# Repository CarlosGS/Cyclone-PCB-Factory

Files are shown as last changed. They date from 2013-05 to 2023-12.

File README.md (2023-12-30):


<p align="center">
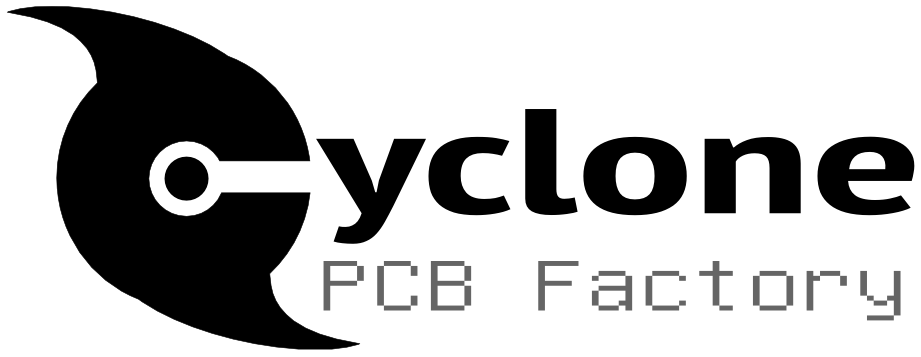
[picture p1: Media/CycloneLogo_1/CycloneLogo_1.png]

<div align="center"><i>A 3D-printable (Rep-Rap alike) CNC machine, intended for PCB manufacture.</i></div>
</p>  

Read this, it's important!
-----------

Please note that this project is no longer active and is of historical interest only.
===========

Check out this thread before printing the parts: <https://github.com/CarlosGS/Cyclone-PCB-Factory/issues/57>

**Also take a look at the following locations:**

- **Releases: <https://github.com/carlosgs/Cyclone-PCB-Factory/releases>**
- **Documentation: <https://github.com/carlosgs/Cyclone-PCB-Factory/wiki>**

<p align="center">
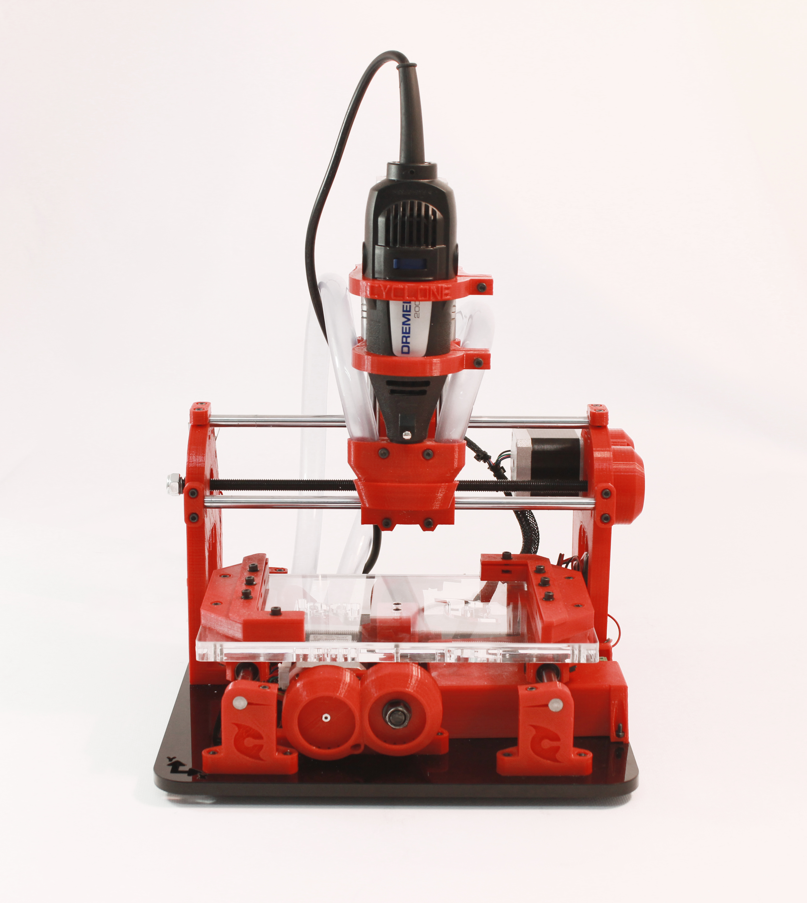
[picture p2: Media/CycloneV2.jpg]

<div align="center"><i>Cyclone v2. Picture by bq</i></div>
</p>

Mail list / Forum  
-------------------
If you are interested in this project, please consider joining our mail list:  
**English: <https://groups.google.com/forum/#!forum/cyclone-pcb-factory>**  
**Spanish/Español: <https://groups.google.com/forum/#!forum/cyclone-pcb-factory-es>**  

Links of interest  
====================
- **[GitHub project network](https://github.com/carlosgs/Cyclone-PCB-Factory/network)** (useful to find the latest work by collaborators)
- **[Wiki entry on RepRap.org](http://reprap.org/wiki/Cyclone_PCB_Factory)**
- **[Joco's Cyclone journey in the mail list](https://groups.google.com/forum/#!topic/cyclone-pcb-factory/o_YzXokpLnA)**
- **[A year of development (Jan/2014)](https://web.archive.org/web/20150627040708/http://carlosgs.es/node/47)** (project evolution during 2013)
- **[List of suppliers](https://github.com/carlosgs/Cyclone-PCB-Factory/wiki/List-of-suppliers)**

Getting the (development) source files  
========================================
Install git (http://git-scm.com/) onto your system. Then run a clone:

	git clone git://github.com/carlosgs/Cyclone-PCB-Factory.git

This will download the latest sources into a directory named 'Cyclone-PCB-Factory'.  

Current stable version: 2.1  
--  

**Recent news:**
* [Kris Wauters](http://www.digitalplayground.be/) has designed [a set of feet](http://www.thingiverse.com/thing:1131591) that raise up the machine and allow to place the electronics underneath. He has also made a [Z endstop support](http://www.thingiverse.com/thing:1131591). Check out his beautiful build in [his blog](http://www.digitalplayground.be/?p=3255).
* Introductory tutorial: [**Milling a bowl with bCNC**](https://github.com/carlosgs/grblForCyclone/wiki/2%29-Hello-World!-Mill-a-bowl-with-bCNC) (**implemented support for GRBL firmware in RAMPS and Sanguinololu** 3D printer electronics. GRBL is better for CNCs than Marlin).
* Released [**Cyclone XL (beta)**](Output_files/Cyclone_XL) with a milling area of **500x250mm**.
* BQ additions have been re-incorporated into the main parametric design (zip-ties in the Y carriage linear bearing holders, longer Z motor gear, same orientation for the Y rod idlers).
* If you use RAMPS, you may want to try this [GRBL mod](https://github.com/carlosgs/grblForCyclone), it is better than Marlin. Control it with the [bCNC](https://github.com/vlachoudis/bCNC) graphical interface.
* Z carriage modified for Dremel 3000 by [Nicolas Arias](https://groups.google.com/forum/#!msg/cyclone-pcb-factory/mfZC0KEy7gw/TaSLBKO9QJUJ) and [Marcos Bladauskas](https://groups.google.com/forum/#!msg/cyclone-pcb-factory/WJLWC5qAm-w/70eSQ2DBCAAJ) ([download it here](Output_files/Zcarriages)).
* Check out the [Arduino CNC shield housing](http://www.thingiverse.com/thing:929981) by Oliver Kreuzenbeck (Helicon).
* [Source code improvements (better parameterization, M4 screw version)](https://github.com/carlosgs/Cyclone-PCB-Factory/pull/33) by [Arne Durr (D-Byte)](https://github.com/D-Byte).
* An [**aluminium spindle holder**](https://github.com/carlosgs/Cyclone-PCB-Factory/pull/40) by [Marc Muntada (quikshot)](https://github.com/quikshot) ([download it here](Output_files/Zcarriages)).
* There is also [a folder](bq_additions) with the version by [Pedro de Oro](https://github.com/PedroDeOro) and [Luis Díaz](http://diwo.bq.com/author/ldiaz/) from **bq**, with some additions that simplify the assembly process (these have already been merged into the main branch).
* Daniel Evrard has [assembled Cyclone in Sketchup](https://groups.google.com/forum/#!msg/cyclone-pcb-factory/1TpFxE7avRo/EBSx7ouy9GwJ) which can be very useful as a template.
* Thanks must also go to [ve3sjk](https://github.com/ve3sjk), [joco-nz](https://github.com/joco-nz), Aisflow, Yiannis Mandravellos, Samuel Kranz and [yOPERO](https://github.com/yOPERO) for their constructive discussions and continuous support.
* If your printer is too small to print the main frames of the machine, take a look at the [**shorter version of the frames**](Output_files/ShorterVersion) (thanks [Burt Bicksler!!](https://groups.google.com/forum/#!msg/cyclone-pcb-factory/ue6NiWs713w/A7_4h4Ynf54J)).

**Cyclone PCB Factory V2.0 was developed in the department of innovation and robotics at [bq](http://www.bq.com/)**  
**V2.0** addressed all the issues from the original design, and implementing improvements by yOPERO, Martin Zabojnik and others:  

* More robust design with tougher parts:
 * Better holders for the linear bearings (vibration made them slide away)
 * Reinforced nut/screw holders
* Anti-backlash mechanisms
* Improved gears with smoother edges
* Protective cover for the gears
* Attachment for a vacuum cleaner
* Better scalability (parameterized design)
* Using a [Dremel 200](http://www.dremel.com/en-us/tools/Pages/ToolDetail.aspx?pid=200+Series) as the spindle motor
* Integrated endstop holders

<p align="center">
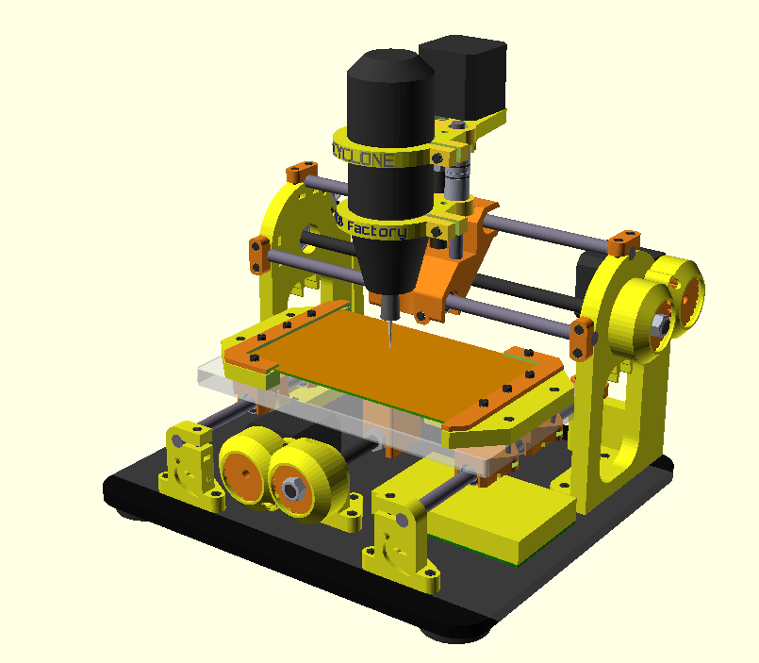
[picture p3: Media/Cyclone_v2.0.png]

<div align="center"><i>Render of Cyclone v2.0</i></div>
</p>  

<p align="center">
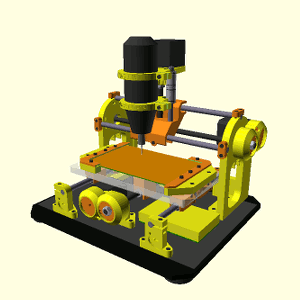
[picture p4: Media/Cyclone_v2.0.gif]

<div align="center"><i>The new design tries to be more parameterized</i></div>
</p>

Videos  
--  
- October 2015. Full milling process with bCNC, by Carlosgs: <https://www.youtube.com/watch?v=tWrt1B1CeP0>
- September 2015. Cyclone PCB jogging and homing test with bCNC, by Ianmcmill: <https://www.youtube.com/watch?v=GqbSjCq_hWg>
- July 2015. v2.0 Milling a PCB, timelapse by Helicon007: <https://www.youtube.com/watch?v=GpFG2Z8Jt-w>
- April 2015. Cyclone PCB Factory belt drive, by Nihilianth: <https://www.youtube.com/watch?v=bdu1vz6ndGs>
- April 2015. Introduction & assembly tips, by Project23D: <https://www.youtube.com/watch?v=0mW087ijIdE>
- v2.0 Plexiglass "Open Source Hardware" keychain: <http://www.youtube.com/watch?v=3Kftgog89wQ>
- v2.0 Cyclone Logo in PCB (October 2014): <http://www.youtube.com/watch?v=_6oWuco_N8U>
- v2.0a Plexiglass Cyclone logo (August 2014): <http://www.youtube.com/watch?v=lPQlIvBf7Ak>
- v2.0a Milling wax (August 2014): <http://www.youtube.com/watch?v=drV_r_OSsi4>
- February 2014. First drawing test with the Cyclone PCB Factory CNC, by Samuel Ureta: <https://www.youtube.com/watch?v=F7SczbShmxA>
- December 2013. Adjustment of Cyclone PCB Factory Y Stepper Motor Current, by Glen Chung: <https://www.youtube.com/watch?v=-TPqWOsY0Ls>
- v0.9.7 Cyclone PCB factory, the process (June 2013): <http://www.youtube.com/watch?v=fKW3fwy1h0k>
- v0.9.6 Y axis concept by yOPERO <http://www.youtube.com/watch?v=XzcobonQP40>
- v0.9.5 Probing a PCB <http://www.youtube.com/watch?v=m5zXL8k5T9E>
- v0.9.5 Milling MDF <http://www.youtube.com/watch?v=2QpxjheEjEc> and <http://www.youtube.com/watch?v=zjav0hBtmYA>
- v0.8 Drawing test: <http://www.youtube.com/watch?v=Y-HSdE89JOM>
- v0.7.5 XY axis test: <http://www.youtube.com/watch?v=9umlq4oHG64>
- v0.7.5 High speed XY test: <http://www.youtube.com/watch?v=H3uYCXryj60>

- October 2015. Evolution of the Cyclone-PCB-Factory GitHub repository (Gource Visualization), by Landon Wilkins: <https://www.youtube.com/watch?v=0ANaGCHkaco>

More pictures  
--  

<p align="center">
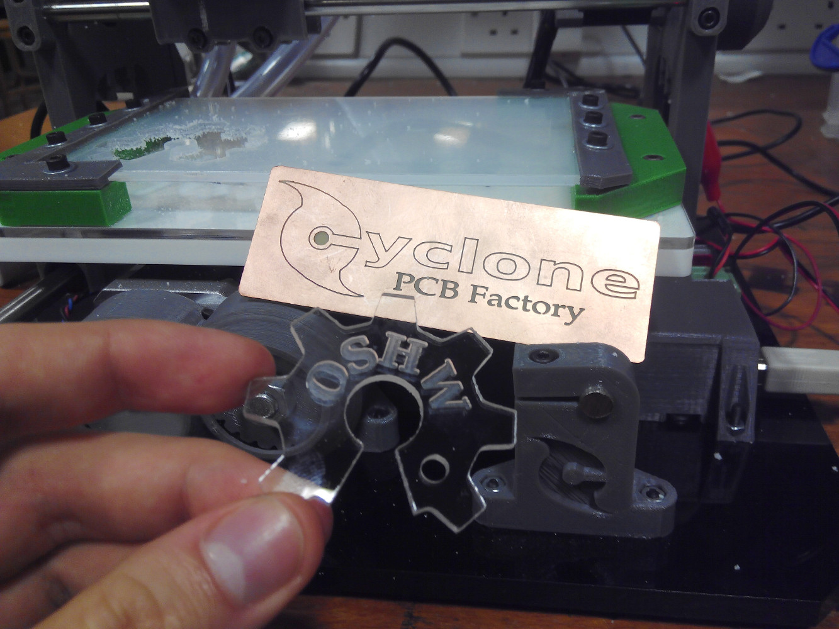
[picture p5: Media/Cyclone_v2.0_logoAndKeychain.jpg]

</p>  

<p align="center">
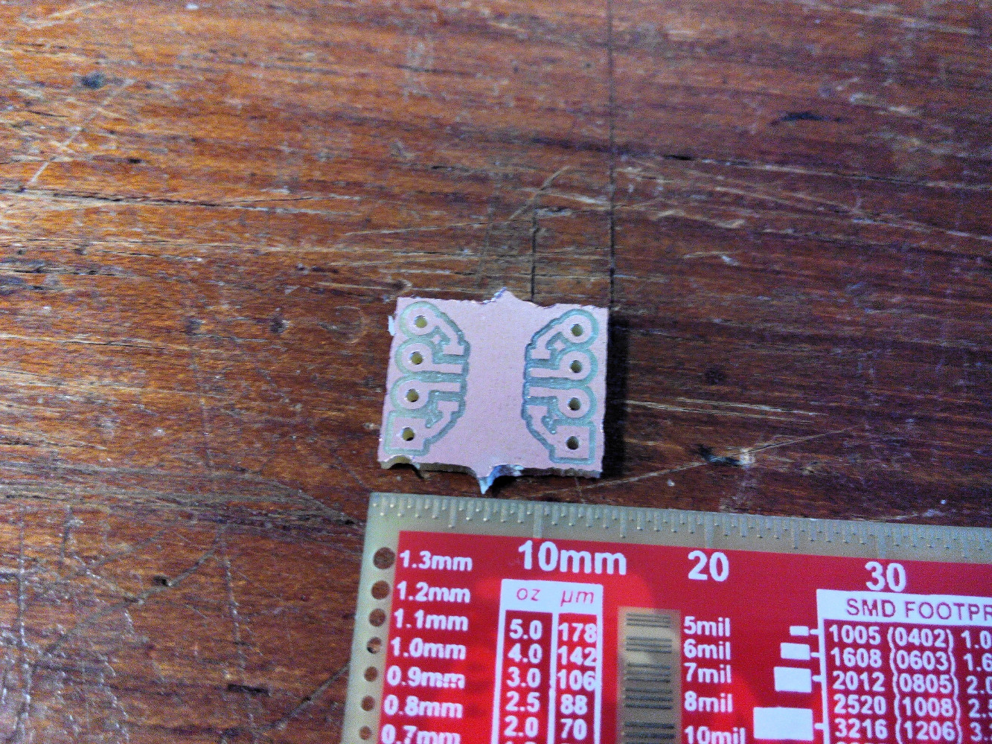
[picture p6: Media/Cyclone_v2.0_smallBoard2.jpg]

</p>  

<p align="center">
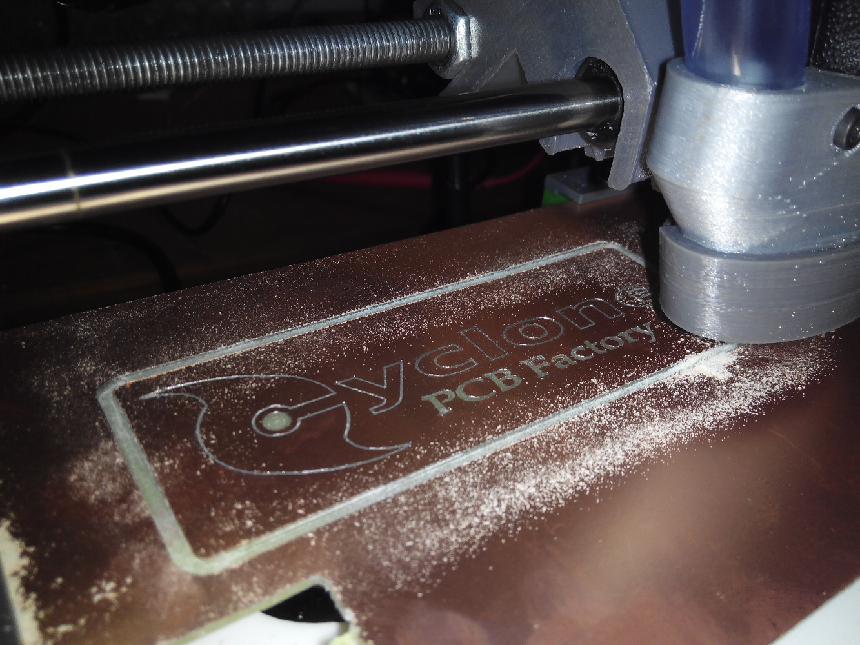
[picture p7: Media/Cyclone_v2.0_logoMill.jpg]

</p>  

<p align="center">
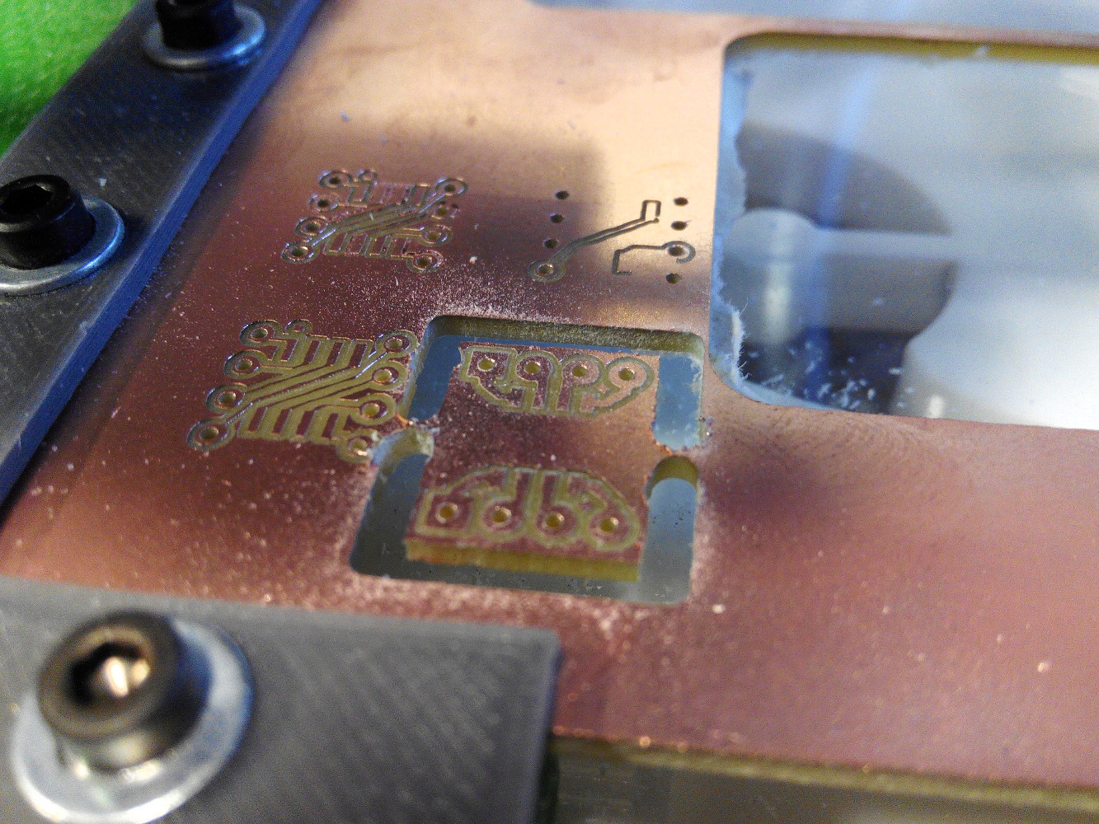
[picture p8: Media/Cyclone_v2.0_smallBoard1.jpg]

</p>  

License  
--
License: **Attribution - Share Alike - Creative Commons (<http://creativecommons.org/licenses/by-sa/3.0/>)**  

Authors:  
--
**Carlos García Saura (<http://github.com/CarlosGS>)** released the project as open-source and is the current maintainer.

**Many other people keeps contributing to the project (check GitHub contributions and "most active posters" at <https://groups.google.com/forum/#!aboutgroup/cyclone-pcb-factory>).**  

Special thanks  
--  
- **Arne Durr (D-Byte)** finished the OpenScad assembly and made the code much more parametric.  
- Plenty of feedback from **Pedro de Oro**, **Alberto Valero**, **Alberto Mendez** (and **Obijuan**, **Pacle**, **Jesus**, **Ana**, **Santi**, **Antonio**, **Jose**... :-P) at the _department of innovation and robotics at [bq](http://www.bq.com/)_. **Cyclone is much more user-friendly thanks to you!**  
- **Glen Chung** (<https://github.com/glenchung>) improved the OpenScad code quite a lot (a much more elegant code), providing a great start point for V2.0.  
- Z axis concepts by **Quim Borras** and the spindle motor holder by **Misan** were really useful!! Also, **Diego Viejo**'s machine was of great inspiration for the Z axis (<https://plus.google.com/u/0/photos/113930344830086538817/albums/5868944432651911713?authkey=CLDJgdehlN773gE>) **Thank you all!!**  
- This design woudn't have been possible without the encouragement of the **Panda CNC community** (<https://plus.google.com/u/0/communities/102402711800402614517>)  
- Also, thanks to **Juan González-Gómez (Obijuan <http://iearobotics.com>)** for naming the machine Cyclone :)  

Derived from / we have used / inspirational  
--
- "Linear actuator concept for CNC machines" by **Carlosgs** (<http://www.thingiverse.com/thing:45103>)  
- "Obiscad library" by **Obijuan** (<https://github.com/Obijuan/obiscad>)  
- "Minimal footprint friction-fit LM8UU holder" by **thantik** (<http://www.thingiverse.com/thing:23041>)  
- "Spindle mount for ShapeOko" by **Misan** (<http://www.thingiverse.com/thing:26740>)  
- "Carro Z para Cyclone CNC mill intended for PCB" by **Quim** (<http://www.thingiverse.com/thing:80718>)  
- "Write.scad (and DXF fonts)" by **HarlanDMii** (<http://www.thingiverse.com/thing:16193>)  
- "PCB Machining Vise" by **Forgetful_Guy** (<http://www.thingiverse.com/thing:63578>)  

Credit for the ideas used  
--  
The origin of Cyclone took place while I (carlosgs) was inside the **Panda CNC** community (<https://plus.google.com/u/0/communities/102402711800402614517>). This is from December 2012 to mid-February 2013.  
Here is the credit for the ideas that were used:  

* _Let's design a 3D-printable CNC for PCB milling, it will be named Panda:_ **Guillermo Welch** (mid-December, via Google Talk)  
* _X carriage rod distribution:_ **César Augusto Fernández Cano** claims Cyclone's X axis is a derivate of his concept: <https://plus.google.com/u/0/111421387442355054591/posts/QrfYtEuZBaj>  
* _100x160mm workspace:_ **David Martin** <https://dl.dropboxusercontent.com/u/16122275/PandaCNC_credit/workplace_size.png>  
* _Using gears to drive the X-Y axes:_ **Guillermo Welch** <https://plus.google.com/u/0/101232926728463427403/posts/QjZGNcWcgGg>  
* _Regarding the woodbase:_ **Guillermo Welch** always contemplated the possibility of attaching the machine (optionally) to a woodbase. I decided to use the base as a main structural part instead. See <https://dl.dropboxusercontent.com/u/16122275/PandaCNC_credit/woodbase.png> (screenshot from <https://plus.google.com/u/0/113437723819360223498/posts/8LDCSSVWqCS>)  
* _List of CNC endmill types:_ **David Martin** <https://dl.dropboxusercontent.com/u/16122275/PandaCNC_credit/cnc_endmill_types.png>  

Please note I have taken screenshots of the post that are on the closed G+ Panda community (<https://plus.google.com/u/0/communities/116318709564872967169>). You can register and see by yourself.  

**All other development present on Cyclone has nothing to do with Panda and is not related to the Panda project.**  

Disclaimer  
--
This hardware/software is provided "as is", and you use the hardware/software at your own risk. Under no circumstances shall any author be liable for direct, indirect, special, incidental, or consequential damages resulting from the use, misuse, or inability to use this hardware/software, even if the authors have been advised of the possibility of such damages.  

Please cite as:
--
Garcia-Saura, C. (2013). Cyclone PCB Factory. GitHub. https://doi.org/10.5281/ZENODO.10442930

Latex / Bibtex citation:
```bibtex
@misc{cyclonepcb2013,
  author = {Garcia-Saura, Carlos},
  title = {Cyclone PCB Factory},
  publisher = {GitHub},
  year = {2013},
  doi = {10.5281/ZENODO.10442930},
  url = {https://doi.org/10.5281/ZENODO.10442930}
}
```

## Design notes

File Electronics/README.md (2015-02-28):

Electronics for Cyclone-PCB-Factory  
===================

Electronic boards (and firmwares) for controlling Cyclone PCB Factory and similar machines  

* (Feb/2015) Samuel Kranz is working in [another iteration](https://groups.google.com/d/msg/cyclone-pcb-factory/YUhSF-1WIsQ/zLMxC9SWfXoJ) of his board

* [Spindle controller by Samuel Kranz](https://github.com/secures92/SpindleControlStick) and [Controller board by Robert Last](https://github.com/robsbots/Cyclone_Pcb):

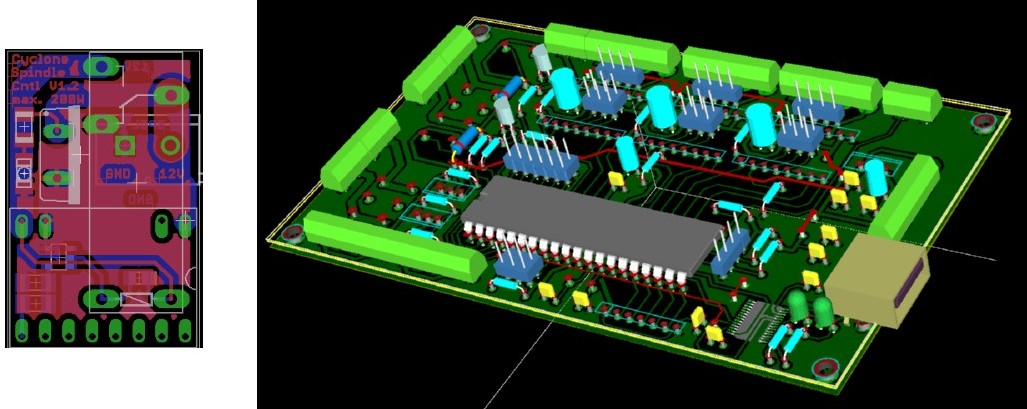
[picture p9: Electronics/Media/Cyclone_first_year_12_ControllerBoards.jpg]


* [GRBL-based controller board by Samuel Kranz](https://github.com/secures92/CyclneGRBLCtrl):

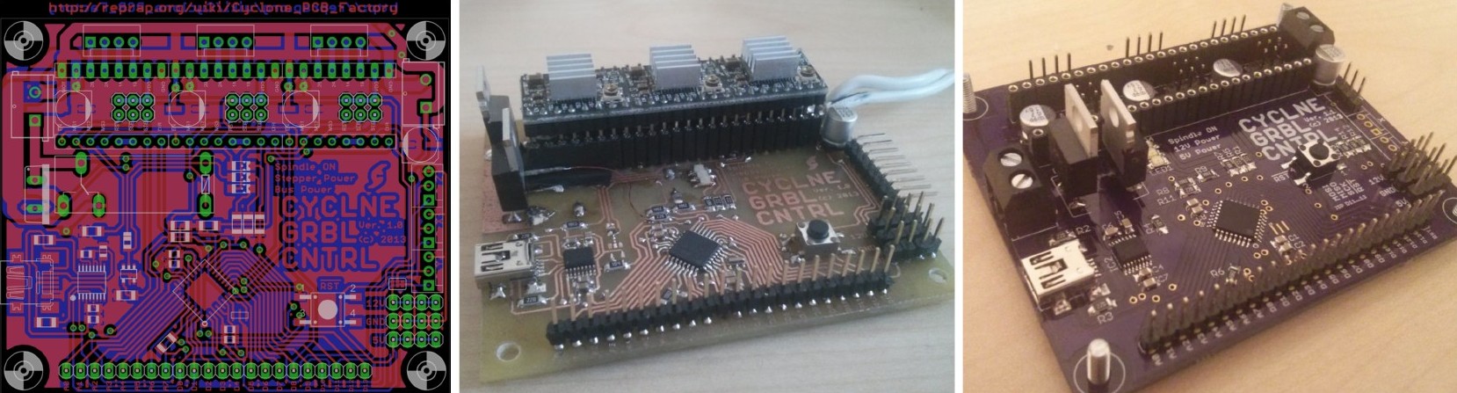
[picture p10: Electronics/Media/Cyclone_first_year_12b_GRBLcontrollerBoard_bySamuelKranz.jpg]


* [CNC Shield by Protoneer](http://blog.protoneer.co.nz/arduino-cnc-shield/) and [CNC Shield box by yOPERO](../Hardware/yOPERO/CNC_shieldBox):

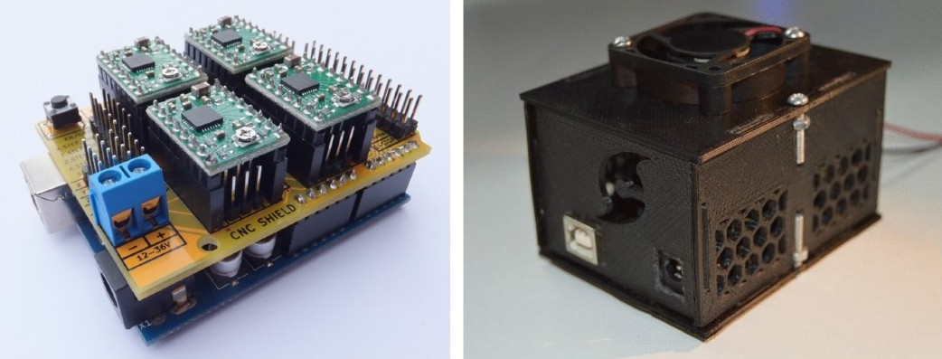
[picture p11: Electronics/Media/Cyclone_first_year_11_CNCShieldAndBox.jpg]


Disclaimer  
--
This hardware/software is provided "as is", and you use the hardware/software at your own risk. Under no circumstances shall any author be liable for direct, indirect, special, incidental, or consequential damages resulting from the use, misuse, or inability to use this hardware/software, even if the authors have been advised of the possibility of such damages.

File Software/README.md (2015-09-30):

Software for Cyclone-PCB-Factory  
===================

**Read <https://github.com/carlosgs/grblForCyclone/wiki> for information regarding the software toolchain.**  

* [Kobus's GUI](https://www.dropbox.com/sh/k7p896n0upv29u1/1T_lcIZDnH/prototypeGui2) ([forum](https://groups.google.com/forum/#!msg/cyclone-pcb-factory/S3m1baPzwRk/DtyngGGJmBoJ)) and [Patrick Knöbel's gcode postprocessor](https://github.com/pknoe3lh/cncgcodecontroller/releases) ([forum](https://groups.google.com/forum/#!msg/cyclone-pcb-factory/ToTGIpXWUmA/gyQMDqDOXfUJ)):

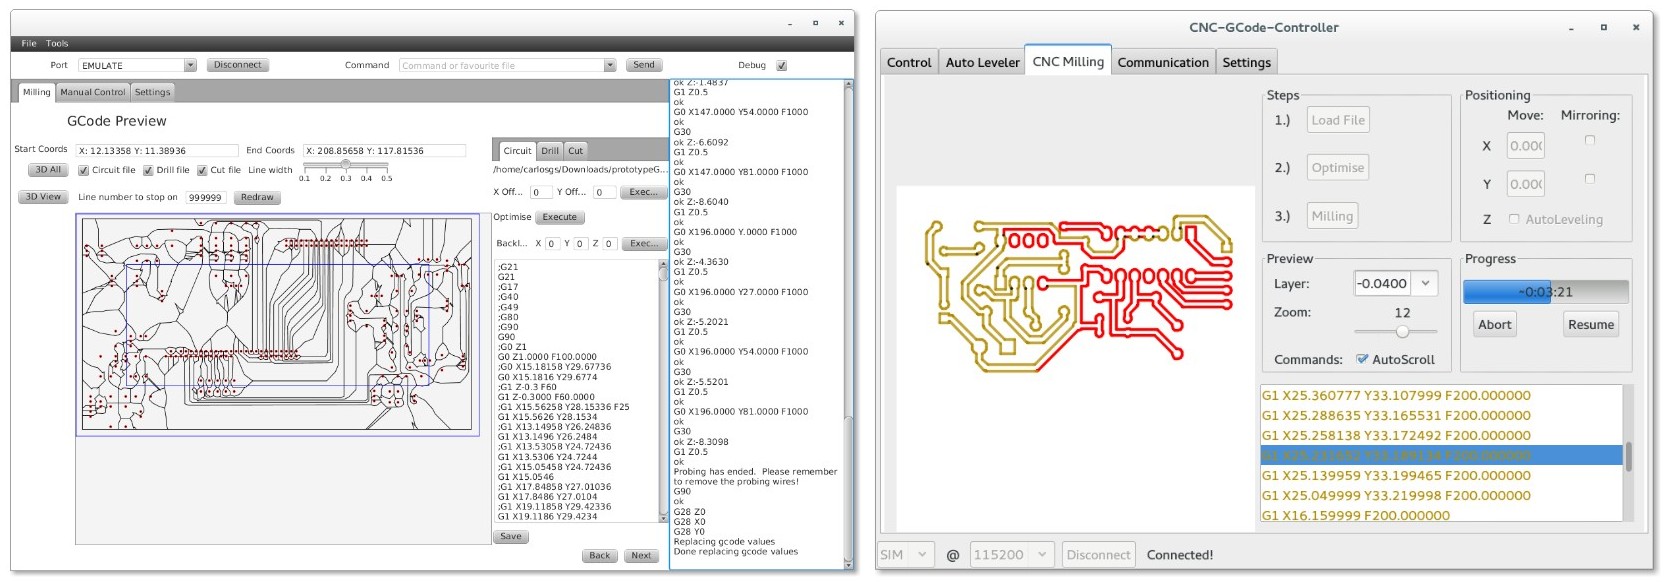
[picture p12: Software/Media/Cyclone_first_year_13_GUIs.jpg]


**A modification of CNC-Gcode-Controller (pre-configured with Cyclone v2.0 parameters) can be downloaded from** <https://github.com/carlosgs/cncgcodecontroller/blob/master/CNC-GCode-Controller_libs.jar?raw=true>  

* [Python scripts by Carlosgs (obsolete)](PythonScripts/):

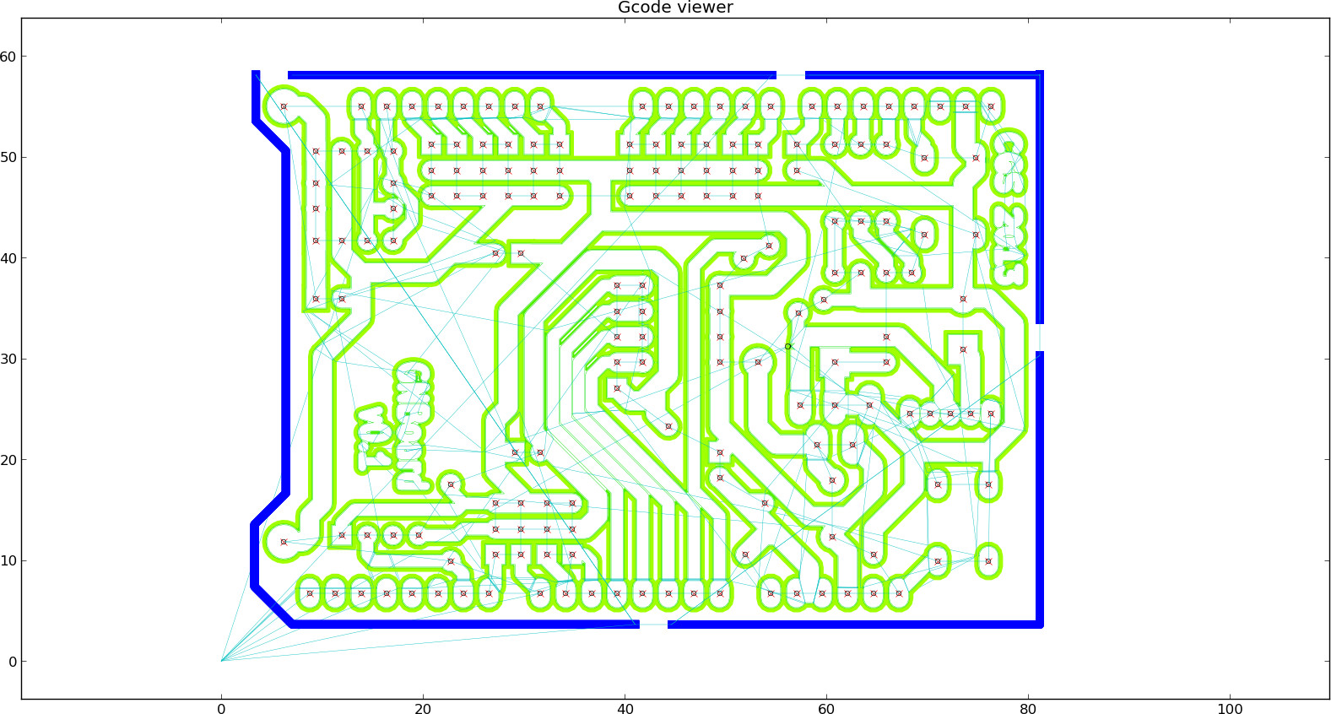
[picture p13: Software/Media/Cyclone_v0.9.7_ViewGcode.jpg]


Disclaimer  
--
This hardware/software is provided "as is", and you use the hardware/software at your own risk. Under nocircumstances shall any author be liable for direct, indirect, special, incidental, or consequential damages resulting from the use, misuse, or inability to use this hardware/software, even if the authors have been advised of the possibility of such damages.

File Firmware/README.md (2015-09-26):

Firmware for Cyclone PCB Factory
===========================

Currently tested with RAMPS-based electronics:  
- **Marlin** (for use with [CNC-Gcode-Controller](https://github.com/pknoe3lh/cncgcodecontroller)): <https://github.com/carlosgs/MarlinForCyclone>  
- **GRBL (recommended)** (for use with [bCNC](https://github.com/vlachoudis/bCNC)): <https://github.com/carlosgs/grblForCyclone>  

Disclaimer  
--
This hardware/software is provided "as is", and you use the hardware/software at your own risk. Under no circumstances shall any author be liable for direct, indirect, special, incidental, or consequential damages resulting from the use, misuse, or inability to use this hardware/software, even if the authors have been advised of the possibility of such damages.

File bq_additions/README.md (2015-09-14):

bq Additions
===========================
The files contained in this folder are part of the Cyclone branch developed at bq's department of innovation by [Pedro de Oro](https://github.com/PedroDeOro). These improvements will be re-implemented in the OpenScad parametric version of Cyclone.

* **Updates**

- **Cycl_Tapa_Electrónica**: Final version.
- **Cycl_engranajeMotorXY**: Nut hollow more deep in to the gear.
- **Cycl_marcoFrontalY**: Added a extension for motor support. This avoid the vibrations transmision on the mechanism.
- **Cycl_marcoIzquierdoX**: Bearing hollow more deep.
- **Cycl_soporteRodamientoLinealYV2**: Added bridle holder and nut holder for easy way to screw.
- **Cyclone_base_8mm_negro**: Added Electronic case drills, new outline design and reference system in the low left corner.
- **Cyclone_workbed_8mm_transparente_bq**: Added bq logo and re-organize and resize logos.
- **Electrodo_Calibracion_Cyclone_doblado**: Added fold.

* **Documentation**

Please visit [Diwo](http://diwo.bq.com/product/cyclone/).

<p align="center">

<div align="center"><i>Cyclone v2.0</i></div>
</p>

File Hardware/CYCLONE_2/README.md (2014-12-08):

Cyclone PCB Factory  

A 3D-printable (Rep-Rap alike) CNC machine, intended for PCB manufacture.  

Read this, it's important!
===========================
If you are reading this, then you are looking at the development version of Cyclone PCB Factory.
This means files may present inconsistencies (dimensions mismatch, lack of tolerances, etc).
If you just want to build the machine, take a look at the following locations:

- **Releases: <https://github.com/carlosgs/Cyclone-PCB-Factory/releases>**
- **Documentation: <http://reprap.org/wiki/Cyclone_PCB_Factory>**

<p align="center">
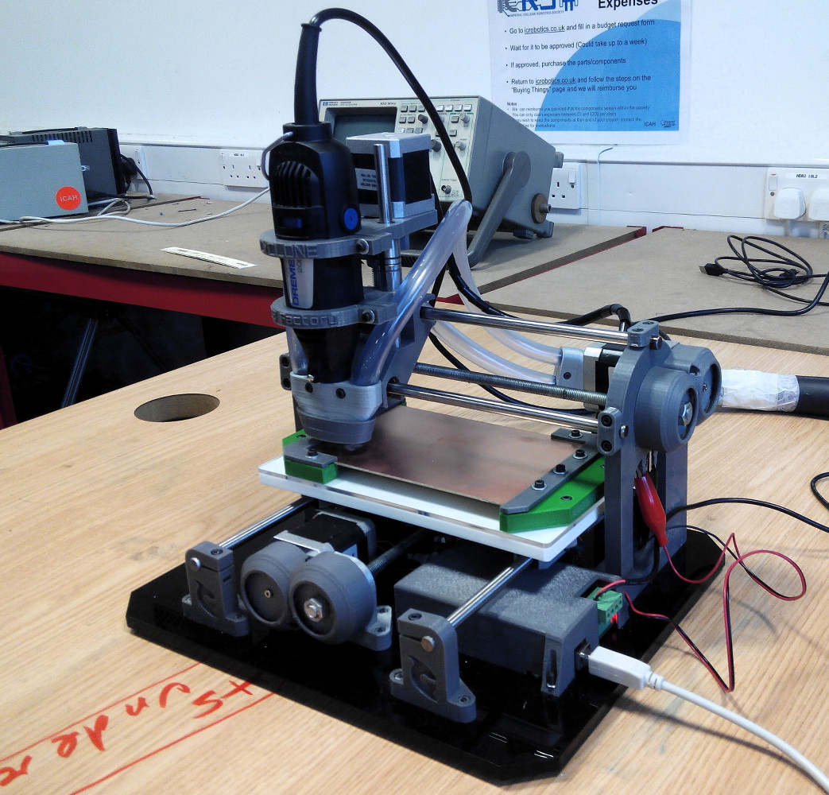
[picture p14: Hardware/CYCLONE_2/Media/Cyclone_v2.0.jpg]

<div align="center"><i>Cyclone v2.0</i></div>
</p>

Mail list / Forum  
-------------------
If you are interested in this project, please consider joining our mail list:  
**<https://groups.google.com/forum/#!forum/cyclone-pcb-factory>**  
Any help and feedback will be appreciated, particularly with software usage and software development :)  

Links of interest  
====================
- **[Project network](https://github.com/carlosgs/Cyclone-PCB-Factory/network)** (useful to find the latest work by collaborators)
- **[Wiki entry on RepRap.org](http://reprap.org/wiki/Cyclone_PCB_Factory)**
- **[A year of development (01/20/2014)](http://carlosgs.es/node/47)** (with information regarding the evolution of the project in 2013)

Getting the (development) source files  
========================================
Install git (http://git-scm.com/) onto your system. Then run a clone:

	git clone git://github.com/carlosgs/Cyclone-PCB-Factory.git

This will download the latest sources into a directory named 'Cyclone-PCB-Factory'.  

Version 2.0  
--  

**Cyclone PCB Factory V2.0 was developed in the department of innovation and robotics at [bq](http://www.bq.com/)**  

V2.0 addresses all the issues from the original design, and implementing improvements by yOPERO, Martin Zabojnik and others.  

* More robust design with tougher parts:
 * Better holders for the linear bearings (vibration made them slide away)
 * Reinforced nut/screw holders
* Anti-backlash mechanisms
* Improved gears with smoother edges
* Protective cover for the gears
* Attachment for a vacuum cleaner
* Better scalability (parametrized design)
* Using a [Dremel 200](http://www.dremel.com/en-us/tools/Pages/ToolDetail.aspx?pid=200+Series) as the spindle motor
* Integrated endstop holders

Future improvements:  
--  
* Endstop integration for Z (integrated probe)
* Re-implement the Z carriage, currently inherited from Cyclone V1

<p align="center">
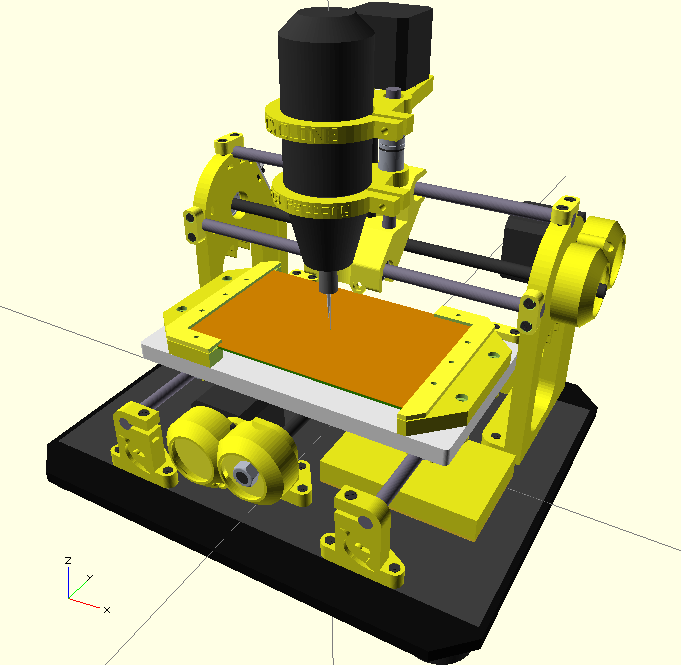
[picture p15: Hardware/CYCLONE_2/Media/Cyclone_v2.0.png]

<div align="center"><i>Render of Cyclone v2.0</i></div>
</p>  

<p align="center">
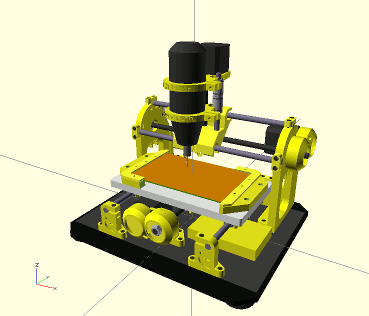
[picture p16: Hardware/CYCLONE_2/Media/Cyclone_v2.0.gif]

<div align="center"><i>The new design tries to be more parametrized</i></div>
</p>

Videos  
--  
- v2.0 Plexiglass "Open Source Hardware" keychain: <http://www.youtube.com/watch?v=3Kftgog89wQ>
- v2.0 Cyclone Logo in PCB (October 2014): <http://www.youtube.com/watch?v=_6oWuco_N8U>
- v2.0a Plexiglass Cyclone logo (August 2014): <http://www.youtube.com/watch?v=lPQlIvBf7Ak>
- v2.0a Milling wax (August 2014): <http://www.youtube.com/watch?v=drV_r_OSsi4>
- v0.9.7 Cyclone PCB factory, the process (June 2013): <http://www.youtube.com/watch?v=fKW3fwy1h0k>
- v0.9.6 Y axis concept by Yopero <http://www.youtube.com/watch?v=XzcobonQP40>  
- v0.9.5 Probing a PCB <http://www.youtube.com/watch?v=m5zXL8k5T9E>  
- v0.9.5 Milling MDF <http://www.youtube.com/watch?v=2QpxjheEjEc> and <http://www.youtube.com/watch?v=zjav0hBtmYA>  
- v0.8 Drawing test: <http://www.youtube.com/watch?v=Y-HSdE89JOM>  
- v0.7.5 XY axis test: <http://www.youtube.com/watch?v=9umlq4oHG64>  
- v0.7.5 High speed XY test: <http://www.youtube.com/watch?v=H3uYCXryj60>  

Bill of materials (obsolete, to be updated and moved to the RepRap wiki page)  
--  
Kobus' <https://docs.google.com/spreadsheet/ccc?key=0AjYcEd1WlkqCdERINEFvRk9mVTZvdXZFR0VHVjRWc2c#gid=0>  
Robsbots' <https://docs.google.com/spreadsheet/ccc?key=0AmiiQRLnjs9cdE12VDFmTHJ4N3JoTzcwbkJPb0ZLSWc#gid=0>  
Carlosgs' <https://docs.google.com/spreadsheet/ccc?key=0AsQp8IK25R4IdGk3LTdOWmpFR0Nrc0RhaVJaUC1CMUE>  

License  
--
License: **Attribution - Share Alike - Creative Commons (<http://creativecommons.org/licenses/by-sa/3.0/>)**  

Authors:  
--
**Carlos García Saura (Carlosgs <http://carlosgs.es>)** is the original author of V2.0.  
**Many other people keeps contributing to the project (check "most active posters" at <https://groups.google.com/forum/#!aboutgroup/cyclone-pcb-factory>).**  

Special thanks  
--  
- Plenty of feedback from **Pedro de Oro**, **Alberto Valero**, **Alberto Mendez** (and **Obijuan**, **Pacle**, **Jesus**, **Ana**, **Santi**, **Antonio**, **Jose**... :-P) at the _department of innovation and robotics at [bq](http://www.bq.com/)_. **Cyclone is much more user-friendly thanks to you!**
- Z axis concepts by **Quim Borras** and the spindle motor holder by **Misan** were really useful!! Also, **Diego Viejo**'s machine was of great inspiration for the Z axis (<https://plus.google.com/u/0/photos/113930344830086538817/albums/5868944432651911713?authkey=CLDJgdehlN773gE>) **Thank you all!!**  
- This design woudn't have been possible without the encouragement of the **Panda CNC community** (<https://plus.google.com/u/0/communities/102402711800402614517>)  
- Also, thanks to **Juan González-Gómez (Obijuan <http://iearobotics.com>)** for naming the machine Cyclone :)  

Derived from / we have used / inspirational  
--
- "Linear actuator concept for CNC machines" by **Carlosgs** (<http://www.thingiverse.com/thing:45103>)  
- "Obiscad library" by **Obijuan** (<https://github.com/Obijuan/obiscad>)  
- "Minimal footprint friction-fit LM8UU holder" by **thantik** (<http://www.thingiverse.com/thing:23041>)  
- "Spindle mount for ShapeOko" by **Misan** (<http://www.thingiverse.com/thing:26740>)  
- "Carro Z para Cyclone CNC mill intended for PCB" by **Quim** (<http://www.thingiverse.com/thing:80718>)  
- "Write.scad (and DXF fonts)" by **HarlanDMii** (<http://www.thingiverse.com/thing:16193>)  
- "PCB Machining Vise" by **Forgetful_Guy** (<http://www.thingiverse.com/thing:63578>)  

Credit for the ideas used  
--  
The origin of Cyclone took place while I (carlosgs) was inside the **Panda CNC** community (<https://plus.google.com/u/0/communities/102402711800402614517>). This is from December 2012 to mid-February 2013.  
Here is the credit for the ideas that were used:  

* _Let's design a 3D-printable CNC for PCB milling, it will be named Panda:_ **Guillermo Welch** (mid-December, via Google Talk)  
* _X carriage rod distribution:_ **César Augusto Fernández Cano** claims Cyclone's X axis is a derivate of his concept: <https://plus.google.com/u/0/111421387442355054591/posts/QrfYtEuZBaj>  
* _100x160mm workspace:_ **David Martin** <https://dl.dropboxusercontent.com/u/16122275/PandaCNC_credit/workplace_size.png>  
* _Using gears to drive the X-Y axes:_ **Guillermo Welch** <https://plus.google.com/u/0/101232926728463427403/posts/QjZGNcWcgGg>  
* _Regarding the woodbase:_ **Guillermo Welch** always contemplated the possibility of attaching the machine (optionally) to a woodbase. I decided to use the base as a main structural part instead. See <https://dl.dropboxusercontent.com/u/16122275/PandaCNC_credit/woodbase.png> (screenshot from <https://plus.google.com/u/0/113437723819360223498/posts/8LDCSSVWqCS>)  
* _List of CNC endmill types:_ **David Martin** <https://dl.dropboxusercontent.com/u/16122275/PandaCNC_credit/cnc_endmill_types.png>  

Please note I have taken screenshots of the post that are on the closed G+ Panda community (<https://plus.google.com/u/0/communities/116318709564872967169>). You can register and see by yourself.  

**All other development present on Cyclone has nothing to do with Panda and is not related to the Panda project.**  

Disclaimer  
--
This hardware/software is provided "as is", and you use the hardware/software at your own risk. Under no circumstances shall any author be liable for direct, indirect, special, incidental, or consequential damages resulting from the use, misuse, or inability to use this hardware/software, even if the authors have been advised of the possibility of such damages.

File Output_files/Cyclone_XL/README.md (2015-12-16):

Cyclone XL (beta)
===========================

<p align="center">
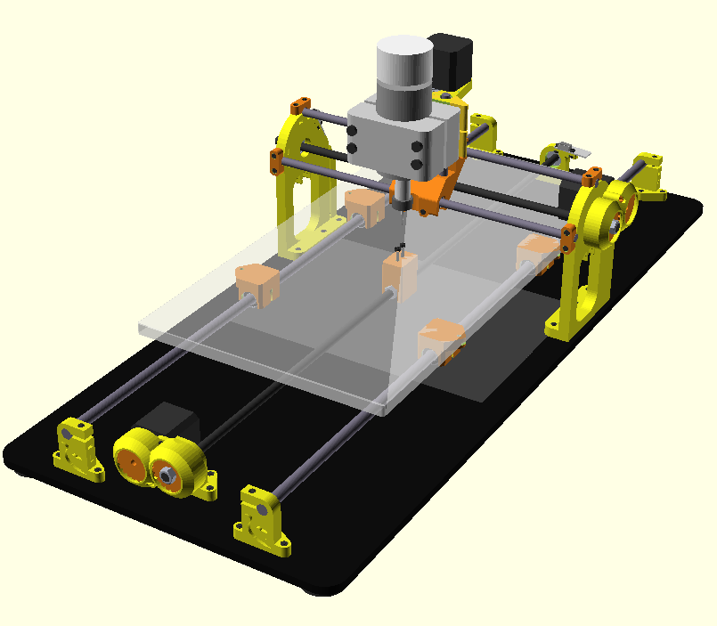
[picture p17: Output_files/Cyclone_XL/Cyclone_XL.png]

<div align="center"><i>Cyclone XL</i></div>
</p>

**Warning: This machine is experimental and may be too wobbly due to the large dimensions involved. Build at your own risk.**

Differences from regular version:  
- Smooth rod lengths: X=340mm Y=770mm (cut them with some additional margin).  
- Note that the Y rods (the long ones) must be M10 rather than M8, and the Y linear bearings LM10UU.  
- Milling area: ~50x25cm  

For the assembly, print templates [A](templates/Cyclone_base_template_A4.pdf) and [B](templates/Cyclone_workbed_template.pdf) to 1:1 scale in A4 paper. This will help you to accurately position the 3D printed parts into the wood bases. Check the [full template](templates/Cyclone_base_template.pdf) for better reference.  

Disclaimer  
--
This hardware/software is provided "as is", and you use the hardware/software at your own risk. Under no circumstances shall any author be liable for direct, indirect, special, incidental, or consequential damages resulting from the use, misuse, or inability to use this hardware/software, even if the authors have been advised of the possibility of such damages.

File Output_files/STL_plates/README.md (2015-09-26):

Last updated: September 26th 2015
---
This plate can serve as a reference on how to print the parts.  
You can also open the STL with [Cura](http://wiki.ultimaker.com/Cura) and use the option "split into parts" to easily re-arrange your own plates.  
In fact, this plate was generated from [the fully assembled STL](../templates/Cyclone.stl).  

Tested Cura slicing settings:  

	Material: PLA, 1.75 mm
	Nozzle diameter: 0.4 mm
	Layer height: 0.25 mm
	Shell thickness: 1.2 mm
	Bottom/Top thickness: 1 mm
	Fill density: 20 %
	Print speed: 60 mm/s
	Printing temperature: 210 deg

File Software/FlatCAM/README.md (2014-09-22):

FlatCAM  
===================

FlatCAM is a neat cross-platform alternative for generating G-codes for PCB milling.  

- <http://caram.cl/software/flatcam/>  
- [User manual](http://caram.cl/software/flatcam-user-manual/)  

The provided [default settings file](defaults.json) simplifies the usage of the program when working with Metric units.  

In order to use these settings, install FlatCAM as usual and afterwards replace the <b>defaults.json</b> file that will be present in the installation folder of FlatCAM.  



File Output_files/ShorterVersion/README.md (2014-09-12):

These parts are shorter, in case you need to print Cyclone with a smaller 3D printer.
They have been generated with

	axes_Xreference_height = 54;

instead of the default value of 74mm.

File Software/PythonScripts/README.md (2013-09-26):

Software for Cyclone-PCB-Factory  
===================

**To-Do list**  
--  
- Create simple program to provide Z probing support for any Gcode
- Graphical User Interface (development in progress in the mail-list)
- Note: The timeout for commands need to be increased.

News  
--
- _TO-DO update this list_
- First Z probing results are promising, read: <https://plus.google.com/u/0/113437723819360223498/posts/9VCHqqnirj6> and <https://plus.google.com/u/0/113437723819360223498/posts/89W2cv1fgQW>  
- Added the python probing script (v0.1) and Octave/Matlab visualizer  

Software: previous existing work  
--  
Here is a compilation of links that have inspired the software controller (specifically the Z probing technique):  

- <http://www.re-innovation.co.uk/web12/index.php/en/blog-75/181-making-pcbs-with-a-cnc-machine>  
- <http://phk.freebsd.dk/CncPcb/>  
- <http://wiki.linuxcnc.org/cgi-bin/wiki.pl?Touch_Probe>  
- <http://things.onshoulders.org/software/PcbSubtraction.php>  
- <http://www.cnczone.com/forums/pcb_milling/82628-cheap_simple_height-probing-5.html>  
- <http://drillcity.stores.yahoo.net/>  
- <http://www.drewtronics.net/>  

- **Examples of the PCB probing method**  
 - onshouldersTv: Open Source Circuit Boards at Home <http://www.youtube.com/watch?v=L-5SRtwx3kY>  
 - PCB routing using the Probe method <http://www.youtube.com/watch?v=fwgT9sCL8fs>  
- <http://pcbgcode.org/>  
- <http://sourceforge.net/apps/mediawiki/pcb2gcode/index.php?title=Main_Page>  
- Very interesting toguether with cam.py: <http://code.google.com/p/pygerber2gcode/>  
- <http://replicat.org/generators>  
- For arranging panels: <http://ruggedcircuits.com/gerbmerge/>  

License  
--
**Attribution - Share Alike - Creative Commons (<http://creativecommons.org/licenses/by-sa/3.0/>)**  

Authors (Software)  
--
- **Carlos García Saura (Carlosgs <http://carlosgs.es>)** (original python scripts)  
- _GUI work in progress by various members of the mail-list_  

Disclaimer  
--
This hardware/software is provided "as is", and you use the hardware/software at your own risk. Under nocircumstances shall any author be liable for direct, indirect, special, incidental, or consequential damages resulting from the use, misuse, or inability to use this hardware/software, even if the authors have been advised of the possibility of such damages.

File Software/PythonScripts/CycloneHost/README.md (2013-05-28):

Cyclone Host  
===================

_**Cyclone host v1.0**_  
 
DESCRIPTION:  
--
Controller for the Cyclone PCB Factory, "a 3D printable CNC machine for PCB manufacture" (http://www.thingiverse.com/thing:49484)  
This software has been tested with a Sanguinololu board running a modified Marlin firmware that supports the G30 probing G-code.  
 
AUTHOR:  
--
Carlosgs (http://carlosgs.es)

LICENSE:  
--
Attribution - Share Alike - Creative Commons (http://creativecommons.org/licenses/by-sa/3.0/)  
 
DISCLAIMER:  
--
This software is provided “as is," and you use the software at your own risk. Under no circumstances shall Carlosgs be liable for direct, indirect, special, incidental, or consequential damages resulting from the use, misuse, or inability to use this software, even if Carlosgs has been advised of the possibility of such damages.  

CREDIT:  
--
This script was created using as a base:  
"Upload GCode to SpereBot" by Tgfuellner http://www.thingiverse.com/thing:9941 (CC-BY-SA)  
Please refer to http://carlosgs.es for more information on this probing method  
 
REQUISITE:  
--
http://pyserial.sourceforge.net  
Installation on Ubuntu: sudo aptitude install python-serial

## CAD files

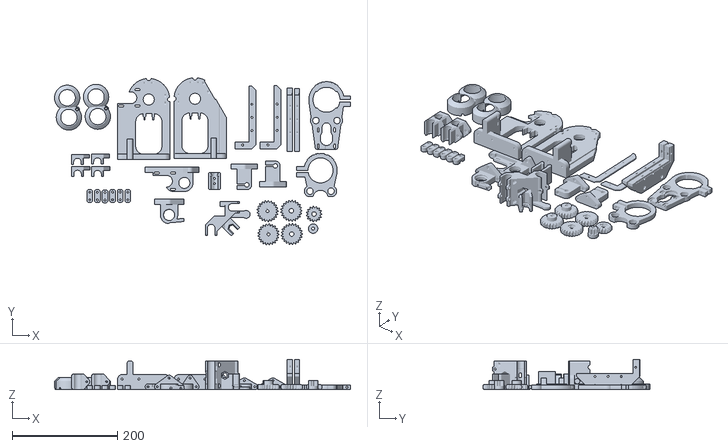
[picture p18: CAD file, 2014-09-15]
Hardware/CYCLONE_2/output/STL_plates/Cyclone_fullPlate.stl
562.7 x 318.1 x 57.5

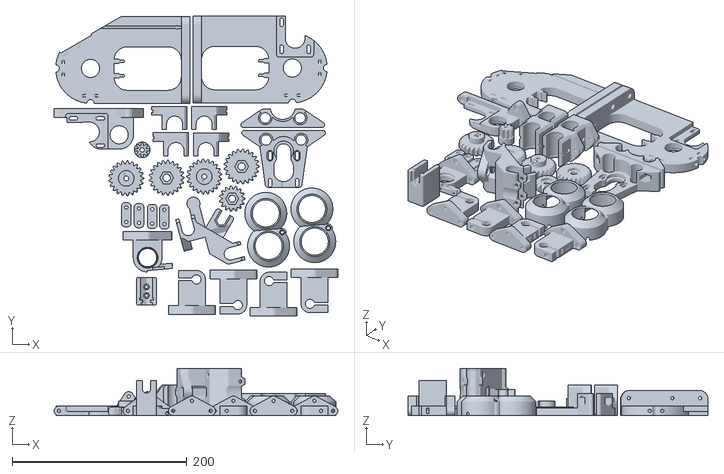
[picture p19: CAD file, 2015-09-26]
Output_files/Cyclone_XL/STL_plates/Cyclone_fullPlate.stl
325.1 x 343.7 x 54.2

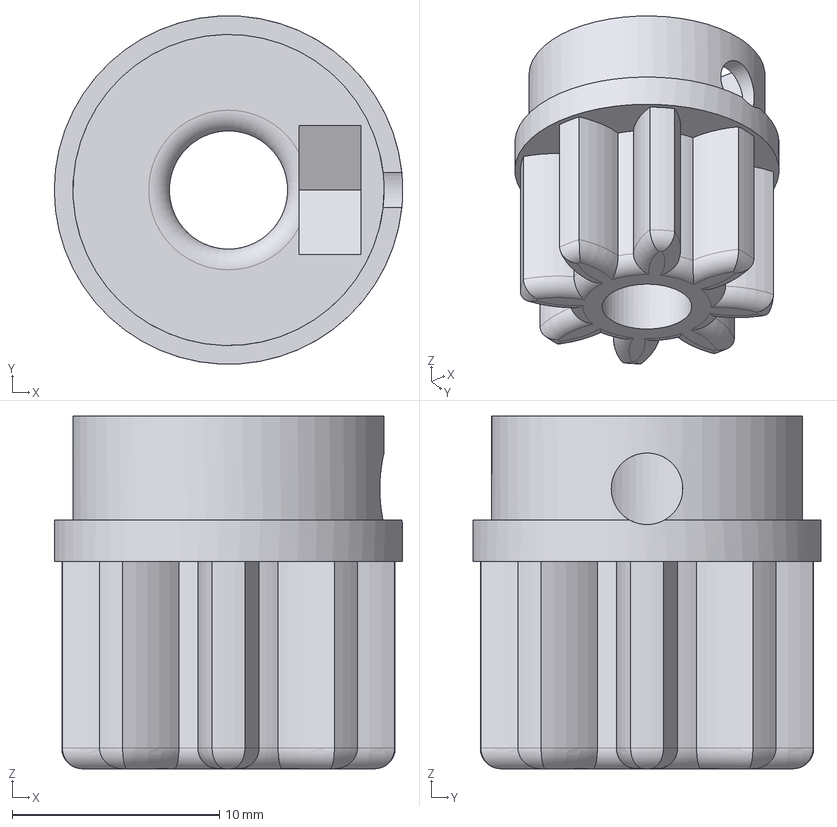
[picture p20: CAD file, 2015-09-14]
bq_additions/Production/STEP/Engranaje_motor_Z.stp
16.8 x 16.8 x 17.0 mm

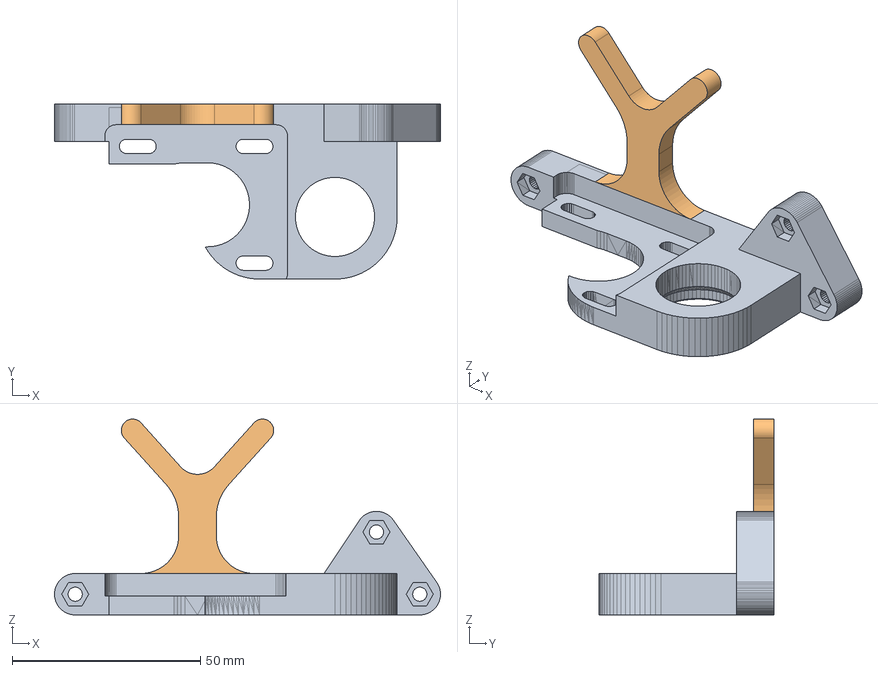
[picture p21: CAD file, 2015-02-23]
bq_additions/Proto/FreeCAD/FrontalY_V2.fcstd
102.5 x 46.5 x 52.0 mm
G004160_Cycl_marcoFrontalY003

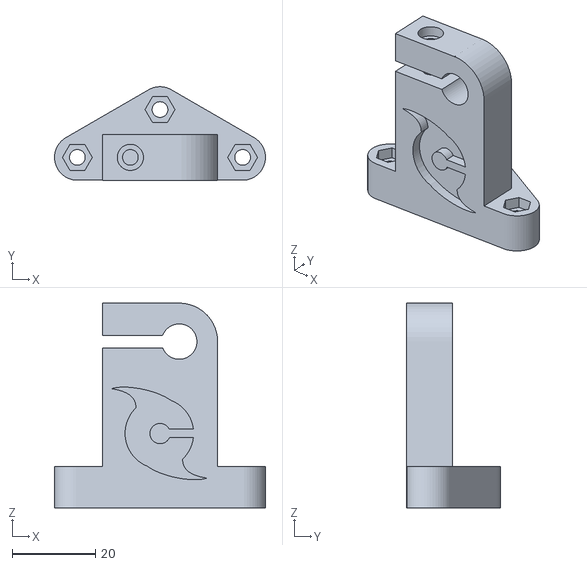
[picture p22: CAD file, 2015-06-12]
bq_additions/Proto/STL/Cycl_soporteYfrenteDerecha.stl
50.8 x 22.5 x 49.2

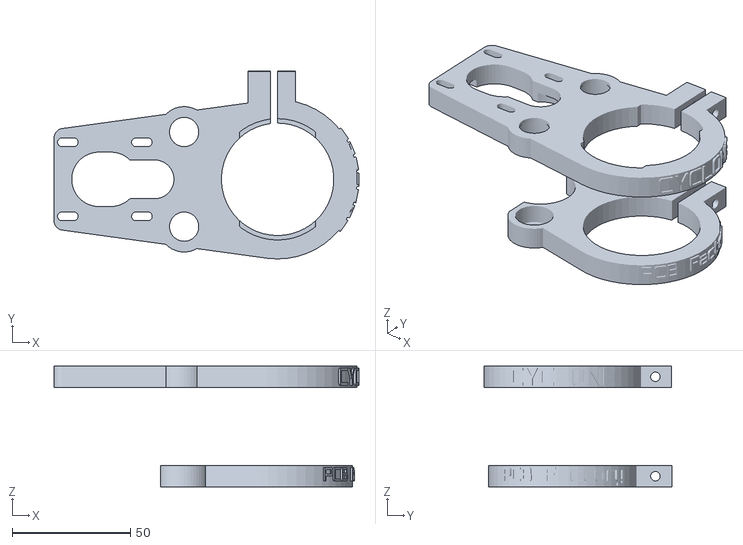
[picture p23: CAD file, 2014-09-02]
Hardware/CYCLONE_2/INHERITED/stl/Z_carriage_mod.stl
128.9 x 79.4 x 51.0

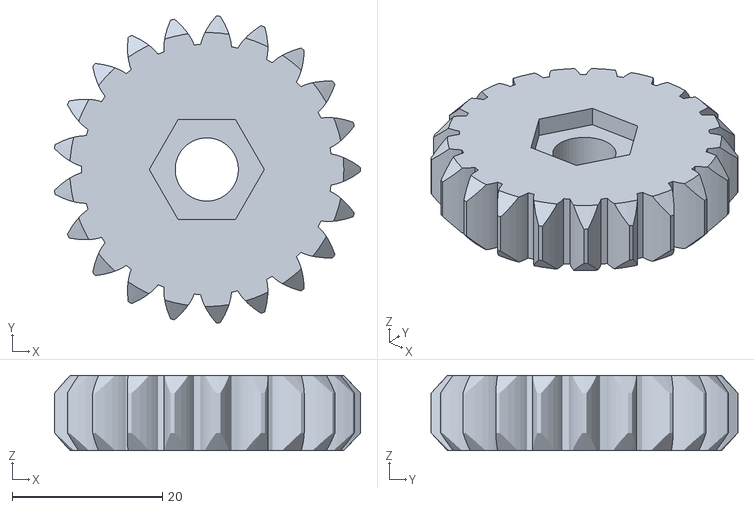
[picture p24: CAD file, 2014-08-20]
Hardware/CYCLONE_2/INHERITED/XYgears/rod_gear.stl
40.7 x 40.8 x 10.0

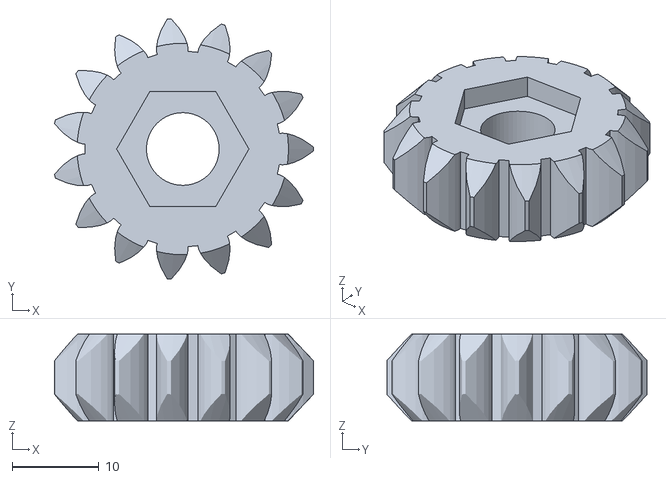
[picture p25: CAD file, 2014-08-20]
Hardware/CYCLONE_2/INHERITED/Zgears/rod_gear.stl
29.9 x 30.1 x 10.0

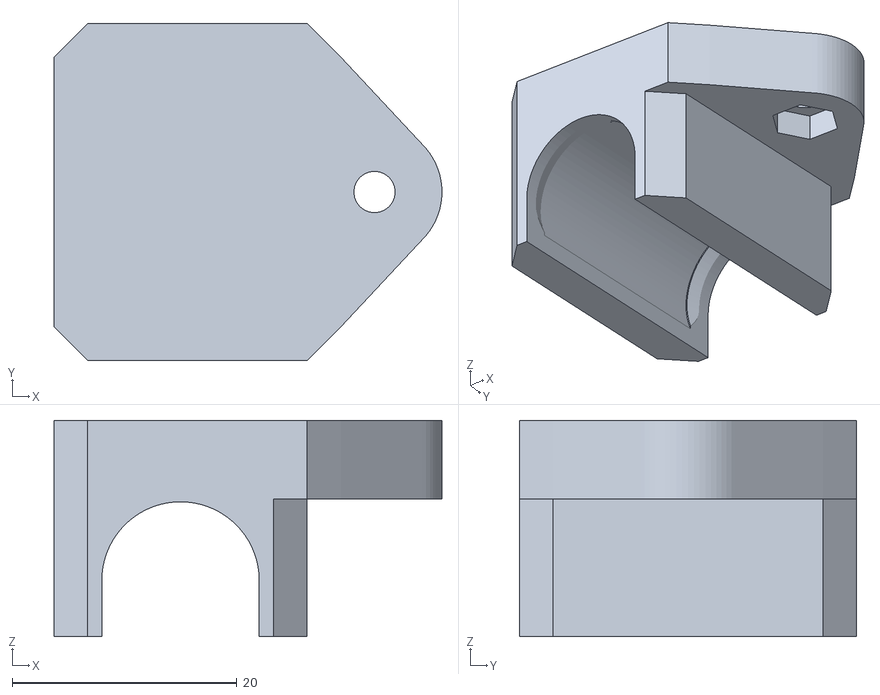
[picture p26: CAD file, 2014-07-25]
Hardware/CYCLONE_2/output/Cyclone_Ycarriage_bearingHolder.stl
34.5 x 30.0 x 19.2

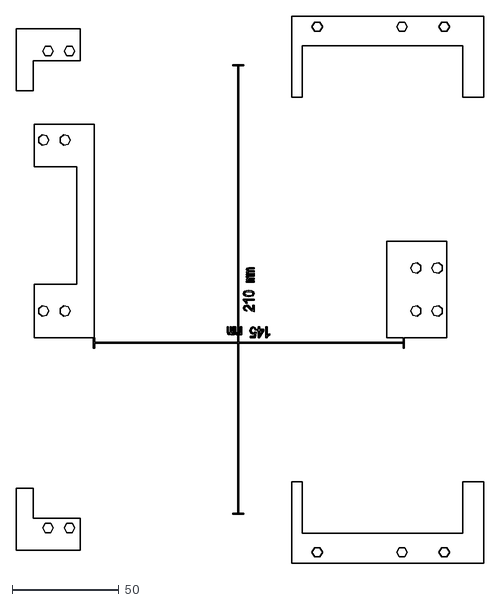
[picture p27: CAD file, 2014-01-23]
Hardware/Development/Cyclone_Template/output/template.dxf
219.0 x 256.0

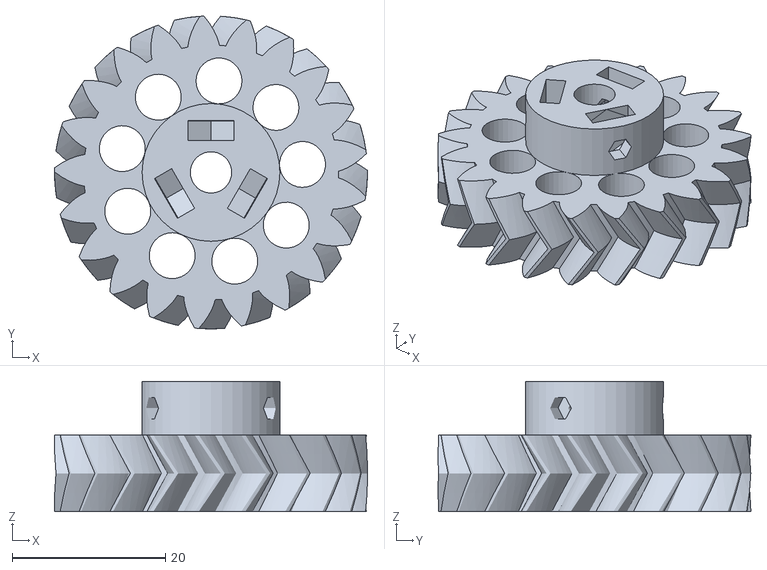
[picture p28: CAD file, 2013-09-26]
Hardware/Development/Gears/stl/motor_gear_21.stl
40.9 x 40.9 x 17.0

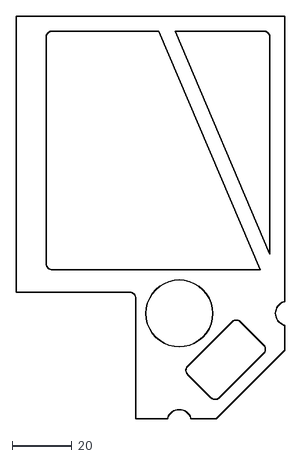
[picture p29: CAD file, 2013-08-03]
Hardware/Development/main_frame/Flat_DXFs/frame_nomotor.dxf
90.0 x 135.0

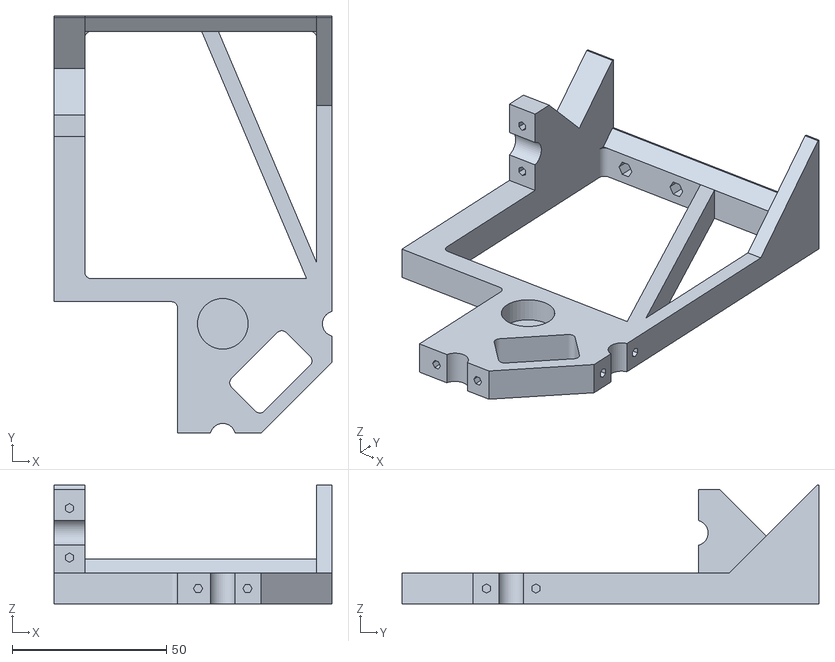
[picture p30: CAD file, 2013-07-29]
Hardware/Development/main_frame/stl/frame_nomotor.stl
90.0 x 135.0 x 38.5

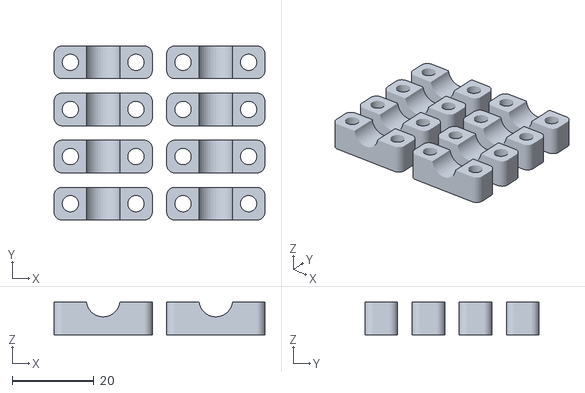
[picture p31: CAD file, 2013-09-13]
Hardware/Development/smooth_rod_fix/stl/smooth_rod_fix_x8.stl
51.5 x 42.5 x 8.00

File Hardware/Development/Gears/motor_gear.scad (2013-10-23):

/* Derived by Carlosgs from:
 * http://www.thingiverse.com/thing:12789
 * An extruder gear set for the TechZone Huxley,
 *  featuring Herringbone teeth.
 * You will have to recalibrate your E_STEPS_PER_MM in
 *  your firmware (ratio changing from original techzone
 *  lasercut gears).
 * This use 2 modules from the MCAD library that you can
 *  get from https://github.com/elmom/MCAD.
 * 
 * Part - the motor gear mount hub with set screw hole -
 *  derived from http://www.thingiverse.com/thing:3104
 *  (thanks GilesBathgate) which is under GPL CC license.
 *
 * Copyright (C) 2011  Guy 'DeuxVis' P.
 *
 * August 2013 added 2 extra setscrews to ensure centered usage.
 * by Harry Binnema. 
 *
 * This program is free software; you can redistribute it and/or
 * modify it under the terms of the GNU General Public License
 * as published by the Free Software Foundation; either version 2
 * of the License, or (at your option) any later version.
 * 
 * This program is distributed in the hope that it will be useful,
 * but WITHOUT ANY WARRANTY; without even the implied warranty of
 * MERCHANTABILITY or FITNESS FOR A PARTICULAR PURPOSE.  See the
 * GNU General Public License for more details.

 * You should have received a copy of the GNU General Public License
 * along with this program; if not, write to the Free Software
 * Foundation, Inc., 51 Franklin Street, Fifth Floor, Boston, MA  02110-1301, USA.
 * -- 
 *     DeuxVis - device@ymail.com */

include <MCAD/materials.scad>
include <MCAD/teardrop.scad>
include <MCAD/involute_gears.scad>

motor_shaft_diameter=5.4;
BigGear_N_Teeth = 21; // 24

nholes = 9; // 7
holes_diam = 6;
hole_distance_from_center = 13.5-4.5+holes_diam/2;

/* Herringbone gear module, adapted from MCAD/involute_gears */
module herringbone_gear( teeth=12, circles=0, shaft=5 ) {
  twist=200;
  height=10;
  pressure_angle=30;

  gear(
    number_of_teeth=teeth,
    circular_pitch=320,
		pressure_angle=pressure_angle,
		clearance = 0.2,
		gear_thickness = height/2,
		rim_thickness = height/2,
		rim_width = 1,
		hub_thickness = height/2,
		hub_diameter=1,
		bore_diameter=shaft,
		circles=circles,
		twist=twist/teeth
  );

	mirror( [0,0,1] )
	  gear(
      number_of_teeth=teeth,
		  circular_pitch=320,
		  pressure_angle=pressure_angle,
		  clearance = 0.2,
		  gear_thickness = height/2,
		  rim_thickness = height/2,
		  rim_width = 1,
		  hub_thickness = height/2,
		  hub_diameter=1,
		  bore_diameter=shaft,
		  circles=circles,
		  twist=twist/teeth
    );
}

module cyclone_motor_gear(with_extra_parts=false, exploded=false) {
// Motor gear
union() difference() {	 
  union() {

    //gear
    herringbone_gear( teeth=BigGear_N_Teeth );

    translate( [0, 0, 12] ) mirror( [0, 0, 1] ) difference() {
      //shaft
      cylinder( r=9, h=15, $fn=40 );
	//adapted to include 3 captive nuts for symmetrical positioning
	//adpted bij HJ Binnema on August 26 2013.
	for (i= [0:2]){
		rotate([0,0,i*120]){
      //captive nut and grub holes
      translate( [0, 20, 3.5] ) rotate( [90, 0, 0] ) union() {
        //enterance
        translate( [0, -3, 14.5] ) cube( [6, 6, 2.6], center=true );
        //nut
        translate( [0, 0, 13.3] ) rotate( [0, 0, 30] )
          cylinder( r=6/2+0.5, h=2.6, $fn=6 );
        //grub hole
        translate( [0, 0, 9] ) cylinder( r=3.2/2, h=10, $fn=6 );
      }}}
    }
  }

  //holes to save plastic
  for(i=[0:nholes-1])
    rotate( [0, 0, i*360/(nholes)+45], $fn=20 )
      translate( [hole_distance_from_center, 0] )
        cylinder( r=holes_diam/2, h=11, center=true, $fn=30 );

  //shaft hole
  translate( [0, 0, -6] ) cylinder( r=motor_shaft_diameter/2, h=20, $fn=30 );
}


  if(with_extra_parts)
    cyclone_motor_gear_extras(exploded_distance=(exploded?20:0));

  module cyclone_motor_gear_extras(exploded_distance=0) {
    echo("Non-Plastic Parts, 1, Grub Screw M3 x 8 mm to attach gear to motor shaft");
    translate([0,2.5+8+exploded_distance,12-3.5])
      rotate([90, 0, 0])
        color(Steel) cylinder(r=1.5, h=8, $fn=30);
  }
}


cyclone_motor_gear();

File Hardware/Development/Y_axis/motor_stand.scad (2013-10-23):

// Cyclone PCB Factory: a 3D printable CNC machine for PCB manufacture
// Created by Carlosgs (http://carlosgs.es)
// License: Attribution - Share Alike - Creative Commons (http://creativecommons.org/licenses/by-sa/3.0/)
// History:
//  - (05/25/2013) Added @yopero's four screw suggestion for the motor stand
//  - (05/28/2013) Added @yopero's four screw suggestion for the idle stand

include <MCAD/stepper.scad>
include <MCAD/bearing.scad>
include <MCAD/metric_fastners.scad>
include <MCAD/nuts_and_bolts.scad>
include <MCAD/materials.scad>
use <../libs/obiscad/bcube.scad>
use <../libs/build_plate.scad>
use <../Gears/rod_gear.scad>
use <../Gears/motor_gear.scad>

motor_width = 43;
motor_length = 49; // not used
motor_screw_distance = 31.3;
motor_center_diameter = 23;

motor_screw_diameter = 3.7;
motor_screw_head_diameter = 8;

motor_adjust_margin = 3;

bearing_diameter = 22.4;
M8_rod_diameter = 8.2;

axis_distance = 32;

wall_thickness = 8;
wall_height = 45;
wall_width = 70;

idler_width = 25;



// For the supports with screws
bottom_thickness = 5;
base_width = 20;
base_length = 20+wall_thickness;
base_screw_diameter = 5;



wall_extraWidth_left = base_width+5;
wall_extraWidth_right = 5;

totalWallWidth = wall_width+wall_extraWidth_left+wall_extraWidth_right;

Cyclone_Nema17 = [
                [NemaModel, 17],
                [NemaLengthShort, 33*mm],
                [NemaLengthMedium, 39*mm],
                [NemaLengthLong, 48*mm],
                [NemaSideSize, 42.30*mm],
                [NemaDistanceBetweenMountingHoles, 31.0*mm],
                [NemaMountingHoleDiameter, 4*mm],
                [NemaMountingHoleDepth, 5.5*mm], //actual is 4.5mm, motor() module is generating 1mm short
                [NemaMountingHoleLip, -1*mm],
                [NemaMountingHoleCutoutRadius, 0*mm],
                [NemaEdgeRoundingRadius, 7*mm],
                [NemaRoundExtrusionDiameter, 22*mm],
                [NemaRoundExtrusionHeight, 1.9*mm],
                [NemaAxleDiameter, 5*mm],
                [NemaFrontAxleLength, 24*mm],
                [NemaBackAxleLength, 15*mm],
                [NemaAxleFlatDepth, 0.5*mm],
                [NemaAxleFlatLengthFront, 15*mm],
                [NemaAxleFlatLengthBack, 14*mm]
         ];


module motorHolesY() {
    // Hole for the motor shaft
    hull() {
      translate([0,motor_adjust_margin/2,0])
        cylinder(r=motor_center_diameter/2,h=10*wall_thickness,center=true,$fn=40);
      translate([0,-motor_adjust_margin/2,0])
        cylinder(r=motor_center_diameter/2,h=10*wall_thickness,center=true,$fn=40);
    }

    // Hole for the screwdriver
    translate([-wall_height/2,0,wall_thickness/2]) rotate([0,90,0]) bcube([2*(wall_thickness-5),5,wall_height],cr=1);

    // Screws for holding the motor
    for(i=[-1,1]) for(j=[-1,1])
    translate([i*motor_screw_distance/2,j*motor_screw_distance/2,2.5-wall_thickness/2]) {
      hull() {
        translate([0,motor_adjust_margin/2,0])
          cylinder(r=motor_screw_diameter/2,h=10*wall_thickness,center=true,$fn=40);
        translate([0,-motor_adjust_margin/2,0])
          cylinder(r=motor_screw_diameter/2,h=10*wall_thickness,center=true,$fn=40);
      }
      hull() {
        translate([0,motor_adjust_margin/2,0])
          cylinder(r=motor_screw_head_diameter/2,h=10*wall_thickness,center=false,$fn=40);
        translate([0,-motor_adjust_margin/2,0])
          cylinder(r=motor_screw_head_diameter/2,h=10*wall_thickness,center=false,$fn=40);
      }
    }
}

module motor_stand_no_base_extras(with_motor=false, exploded_distance=0) {
  // --- additional parts for assembly instruction ---
  if(with_motor) {
    translate([motor_width/2,motor_width/2,0]) {
      rotate([0,180,0])
        translate([0,0,-1+exploded_distance])
          motor(Cyclone_Nema17, NemaLengthLong);
	  echo("Non-Plastic Parts, 1, Nema 17 for Y axis");

      // --- Motor Gear ---
      translate([0,0,12+5.5+exploded_distance])
        rotate([180, 0, -90])
          cyclone_motor_gear(with_extra_parts=true, exploded=(exploded_distance!=0));
    }

    translate([motor_width/2,motor_width/2,wall_thickness/2]) {
      rotate([0,0,15]) translate([0,axis_distance,2.5-wall_thickness/2]) {
        echo("Non-Plastic Parts, 1, Bearing 608 for motor stand");
        translate([0,0,0.5*exploded_distance])
          bearing(model=608);

        // --- Rod Gear ---
        translate([0,0,1.5-wall_thickness/2+5+2.5+7+3+1.5*exploded_distance])
          rotate([0,180,15])
            cyclone_rod_gear(with_extra_parts=true, exploded=(exploded_distance!=0));
      }
    }

    echo("Non-Plastic Parts, 4, Bolt M3 x 6 mm to attach motor on motor_stand");
    for(i=[-1,1]) for(j=[-1,1])
      translate([motor_width/2,motor_width/2,wall_thickness/2])
        translate([i*motor_screw_distance/2,j*motor_screw_distance/2,2.5-wall_thickness/2+exploded_distance*0.7]) {
          rotate([0,180,0]) color(Steel) boltHole(size=3, length=6);
    }
  }

  if(!with_motor) {
    translate([motor_width/2,motor_width/2,wall_thickness/2])
      rotate([0,0,15]) translate([0,axis_distance,2.5-wall_thickness/2]) color(Steel) {
        echo("Non-Plastic Parts, 1, Bearing 608 for idle stand");
        translate([0,0,0.3*exploded_distance]) bearing(model=608);

        echo("Non-Plastic Parts, 1, Washer M8 for idle stand");
        translate([0,0,7+0.6*exploded_distance]) washer(8);

        echo("Non-Plastic Parts, 1, Nut M8 to attach threaded rod on idle stand");
        translate([0,0,6.4+7+0.8+0.9*exploded_distance]) rotate([0,180,0]) flat_nut(8);
      }
  }
}

module motor_stand_no_base(with_motor=true, with_extra_parts=false, exploded=false) {

  if(with_extra_parts)
    motor_stand_no_base_extras(with_motor=with_motor, exploded_distance=(exploded?30:0));

difference() {
  translate([wall_height/2,totalWallWidth/2-wall_extraWidth_left,wall_thickness/2])
    bcube([wall_height,totalWallWidth,wall_thickness],cr=4,cres=10);

  // Position relative to motor shaft
  translate([motor_width/2,motor_width/2,wall_thickness/2]) {

    if(with_motor)
      motorHolesY();

    // Bearing holes
    rotate([0,0,15]) translate([0,axis_distance,2.5-wall_thickness/2]) {
      cylinder(r=(M8_rod_diameter*2)/2,h=10*wall_thickness,center=true,$fn=40);
      cylinder(r=bearing_diameter/2,h=10*wall_thickness,center=false,$fn=60);
    }

  } // End of translate relative to motor shaft
} // End of difference
}

module holder(h=35,noScrews=false,base_width_inc=0, with_extra_parts=false, exploded=false) {
    difference() {
      union() {
        translate([wall_height-bottom_thickness,0]) {
          if(!noScrews) cube([bottom_thickness,base_width+base_width_inc,base_length]);
          hull() {
            cube([bottom_thickness,5,base_length]);
            translate([-h,0,0])
              cube([0.001,5,0.001]);
          }
        }
      }
      // --- screws for the base ---
      if(!noScrews) translate([wall_height,base_width/2+2.5,base_length/1.5])
        rotate([0,90,0]) {
          translate([-5,0,0])
            cylinder(r=base_screw_diameter/2,h=100,center=true,$fn=7);
          translate([5,0,0])
            cylinder(r=base_screw_diameter/2,h=100,center=true,$fn=7);
        }
    } // End of difference
}

module motor_stand(with_motor=true, with_extra_parts=false, exploded=false) {
  union() {
    motor_stand_no_base(with_motor=with_motor, with_extra_parts=with_extra_parts, exploded=exploded);
    translate([0,wall_width]) holder(noScrews=true, with_extra_parts=false, exploded=exploded);
    translate([0,52.4-5/2]) holder(h=12,base_width_inc=1, with_extra_parts=with_extra_parts, exploded=exploded);
    translate([0,-wall_extraWidth_left+base_width]) scale([1,-1,1]) holder(with_extra_parts=with_extra_parts, exploded=exploded);
  }
  if(with_extra_parts && with_motor) {
    translate([0,52.4-5/2])
      idle_stand_extras(exploded_distance=(exploded?17:0));
    translate([0,-wall_extraWidth_left+base_width]) scale([1,-1,1])
      idle_stand_extras(exploded_distance=(exploded?17:0));
  }
}


module idle_stand(with_extra_parts=false, exploded=false) {
	union() {
		intersection() { // Remove the motor part
			motor_stand(with_motor=false, with_extra_parts=with_extra_parts, exploded=exploded);
           union() {
			  translate([wall_height/2,wall_width/2+52.4-(wall_width+wall_extraWidth_right-52.4),wall_thickness/2])
			    bcube([wall_height,wall_width,100],cr=4,cres=10);
			  translate([wall_height/2,wall_width/2+52.4-(wall_width+wall_extraWidth_right-52.4),wall_thickness/2])
			    bcube([wall_height*2,wall_width/6,100],cr=4,cres=10); //keep self tapping screw
           }
		}
		translate([0,wall_width+5-2*(wall_width+wall_extraWidth_right-52.4)]) holder(noScrews=true, with_extra_parts=with_extra_parts, exploded=exploded);
		translate([0,52.4+5/2]) scale([1,-1,1]) holder(h=15,base_width_inc=1, with_extra_parts=with_extra_parts, exploded=exploded);
	}
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

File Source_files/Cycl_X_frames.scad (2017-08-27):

// This file is part of Cyclone PCB Factory: an open-source 3D printable CNC machine for PCB manufacture
// http://reprap.org/wiki/Cyclone_PCB_Factory
// Original author: Carlosgs (http://carlosgs.es)
// License: CC BY-SA 4.0 (Attribution-ShareAlike 4.0 International, http://creativecommons.org/licenses/by-sa/4.0/)
// Designed with http://www.openscad.org/

X_motorModel = Nema17;	
Xmotor_sideLen = lookup(NemaSideSize, X_motorModel); //42.20;
axes_XgearRatio = X_motorGearRatio/X_rodGearRatio; // Number of tooth (motor/rod)

module Cyclone_X_leftFrame() {
	scale([-1,1,1]) Cyclone_X_rightFrame(isLeft=true);
}

include <libs/MCAD/stepper.scad>
module Cyclone_X_rightFrame(isLeft=false) {

	footThickness = X_frame_footThickness;
	corner_radius = X_frame_corner_radius;
	frameFrontalThickness = X_frame_FrontalThickness;
	
	footScrewSize = X_Frame_footScrewSize;
	rodScrewSize = X_Frame_rodScrewSize;
	
	motorWallSeparation = X_motorWallSeparation;
	motorRotatedOffset = X_motorRotatedOffset;
	gearWallSeparation = X_gearWallSeparation;
	
	partThickness = X_frames_additional_thickness+rodScrewSize*2;
	
	dimX = partThickness;
	dimY = axes_Xsmooth_separation+axes_XgearSeparation*cos(motorRotatedOffset)+Xmotor_sideLen/2+1.6;
	dimZ = axes_Yreference_height+axes_Xreference_height+axes_Xsmooth_separation;
	
	footSeparation = footScrewSize*3;
	footWidth = dimX+2*footSeparation;
	
	rodNutSize = X_threaded_rodNutSize;
	rod_nut_len = METRIC_NUT_THICKNESS[rodNutSize];
	nut_separation = rod_nut_len/2;
  //rod_nut_len = 0.8*axes_Xthreaded_rodD;
	
	module Cyclone_XsubPart_gearCover() {
		margin = gearCover_margin;
		rodGearAddedMargin = rodGearAddedgearCover_margin;
		effectiveXgearSeparation = axes_XgearSeparation+0.5;
		wallThickness = gearCover_wallThickness;
		screwHeadSpaceHeight = gearCover_screwHeadSpaceHeight;
		screwHeadSpaceDiam = gearCover_screwHeadSpaceDiam;
		coverHeight = gearCoverHeight;
		coverExtraHeight = gearCoverExtraHeight;
		coverExtraRadius = gearCoverExtraRadius;
		nema_screw_separation = lookup(NemaDistanceBetweenMountingHoles, X_motorModel);
		truncationAngle = gearCover_truncationAngle;
	
		motorGearRadius = axes_XgearSeparation/(1+axes_XgearRatio)+gearCover_margin;
		rodGearRadius = axes_XgearSeparation/(1+1/axes_XgearRatio)+gearCover_margin+rodGearAddedgearCover_margin;
		
		difference() {
			union() {
				// Cover for the rod gear
				rotate([0,90,0])
					cylinder(r=rodGearRadius+gearCover_wallThickness, h=coverHeight);
				translate([coverHeight,0,0])
					rotate([0,90,0])
						cylinder(r1=rodGearRadius+gearCover_wallThickness, r2=rodGearRadius+gearCover_wallThickness+coverExtraRadius, h=coverExtraHeight+gearCover_wallThickness);
				// Translate to motor position
				rotate([motorRotatedOffset,0,0]) {
					translate([0,effectiveXgearSeparation,0])
						rotate([-motorRotatedOffset,0,0]) {
							// Cover for the motor gear
							rotate([0,90,0]) cylinder(r=motorGearRadius+gearCover_wallThickness, h=coverHeight);
							translate([coverHeight,0,0])
								rotate([0,90,0]) cylinder(r1=motorGearRadius+gearCover_wallThickness, r2=motorGearRadius+gearCover_wallThickness+coverExtraRadius, h=coverExtraHeight+gearCover_wallThickness);
							// Cylinder for the support screw
							translate([0,-nema_screw_separation/2,nema_screw_separation/2])
								rotate([0,90,0]) cylinder(r=gearCover_screwHeadSpaceDiam/2+gearCover_wallThickness, h=coverHeight);
						}
				}
			}
			translate([-0.02,0,0])
				union() {
					// Truncation for avoiding collisions with Y carriage (needed for the Y gear cover)
					translate([0,-rodGearRadius/2,-rodGearRadius-0.5])
						rotate([0,90+gearCover_truncationAngle,0]) cube(rodGearRadius);
					// Hole for the rod gear
					rotate([0,90,0])
						cylinder(r=rodGearRadius, h=coverHeight);
					translate([coverHeight-0.02,0,0])
						rotate([0,90,0])
							cylinder(r1=rodGearRadius, r2=rodGearRadius+coverExtraRadius, h=coverExtraHeight);
					rotate([0,90,0])
						cylinder(r=rodGearRadius+coverExtraRadius, h=coverHeight+coverExtraHeight+gearCover_wallThickness+0.1);
					// Translate to motor position
					rotate([motorRotatedOffset,0,0]) {
						translate([0,effectiveXgearSeparation,0])
							rotate([-motorRotatedOffset,0,0]) {
								difference() {
									union() {
										// Hole for the motor gear
										rotate([0,90,0]) cylinder(r=motorGearRadius, h=coverHeight);
										translate([coverHeight-0.02,0,0])
											rotate([0,90,0]) cylinder(r1=motorGearRadius, r2=motorGearRadius+coverExtraRadius, h=coverExtraHeight);
										rotate([0,90,0]) cylinder(r=motorGearRadius+coverExtraRadius, h=coverHeight+coverExtraHeight+gearCover_wallThickness+0.1);
										// Outer hole for the support screw
										translate([0,-nema_screw_separation/2,nema_screw_separation/2])
											rotate([0,90,0]) cylinder(r=gearCover_screwHeadSpaceDiam/2, h=coverHeight+coverExtraHeight*2);
									}
									// Support screw holder
									translate([0,-nema_screw_separation/2,nema_screw_separation/2])
										rotate([0,90,0]) cylinder(r=gearCover_screwHeadSpaceDiam/2+gearCover_wallThickness, h=gearCover_wallThickness);
								}
								// Inner hole for the support screw
								translate([0,-nema_screw_separation/2,nema_screw_separation/2])
									rotate([0,90,0]) cylinder(r=(X_Frame_footScrewSize+1)/2, h=coverHeight+0.1);
								// Holes for the other three screws
								translate([0,nema_screw_separation/2,nema_screw_separation/2])
									rotate([0,90,0]) cylinder(r=gearCover_screwHeadSpaceDiam/2, h=gearCover_screwHeadSpaceHeight/2);
								translate([gearCover_screwHeadSpaceHeight/2,nema_screw_separation/2,nema_screw_separation/2])
									rotate([0,90,0]) sphere(r=gearCover_screwHeadSpaceDiam/2);
								
								translate([0,nema_screw_separation/2,-nema_screw_separation/2])
									rotate([0,90,0]) cylinder(r=gearCover_screwHeadSpaceDiam/2, h=gearCover_screwHeadSpaceHeight/2);
								translate([gearCover_screwHeadSpaceHeight/2,nema_screw_separation/2,-nema_screw_separation/2])
									rotate([0,90,0]) sphere(r=gearCover_screwHeadSpaceDiam/2);
								
								translate([0,-nema_screw_separation/2,-nema_screw_separation/2])
									rotate([0,90,0]) cylinder(r=gearCover_screwHeadSpaceDiam/2, h=gearCover_screwHeadSpaceHeight/2);
								translate([gearCover_screwHeadSpaceHeight/2,-nema_screw_separation/2,-nema_screw_separation/2])
									rotate([0,90,0]) sphere(r=gearCover_screwHeadSpaceDiam/2);
							}
					}
				}
		}
	}
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

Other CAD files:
bq_additions/Proto/CAD/#Cyclone_base_8mm_negro.dxf
Hardware/Development/XZ_axis/stl/Z_carriage_bottom.stl
Hardware/Development/Y_axis/stl/idle_stand.stl
Hardware/XZ_axis/stl/Z_carriage.stl
Hardware/Development/XZ_axis/motor_gear.scad
Hardware/CYCLONE_2/INHERITED/XYgears/rod_gear.scad
Hardware/CYCLONE_2/INHERITED/Z_carriage_mod.scad
Hardware/CYCLONE_2/INHERITED/Zgears/rod_gear.scad
Hardware/Development/Cyclone_Template/output/Cyclone.stl
Hardware/Development/Gears/rod_gear.scad
Hardware/Development/Gears/stl/rod_gear_15.stl
Hardware/Development/XZ_axis/X_carriage.scad
Hardware/Development/XZ_axis/Z_carriage.scad
Hardware/Development/XZ_axis/Z_carriage_old.scad
Hardware/Development/XZ_axis/rod_gear.scad
Hardware/Development/XZ_axis/stl/X_carriage.stl
Hardware/Development/XZ_axis/stl/Z_carriage_top.stl
Hardware/Development/Y_axis/Y_nut_holder.scad
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

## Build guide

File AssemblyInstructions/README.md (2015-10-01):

[Link to the instructions in the wiki](https://github.com/carlosgs/Cyclone-PCB-Factory/wiki)

Credits
--
[Original instructions](http://diwo.bq.com/como-montar-cyclone-paso-a-paso/) by **bq**.  
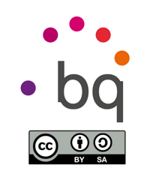
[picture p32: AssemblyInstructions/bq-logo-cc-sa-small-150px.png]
CC-BY-SA
  
License: **Attribution - Share Alike - Creative Commons (<http://creativecommons.org/licenses/by-sa/4.0/>)**

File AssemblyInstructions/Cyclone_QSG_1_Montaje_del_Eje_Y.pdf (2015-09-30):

1

# Montaje del Eje Y

### BQ Cyclone

1 Preparar los marcos laterales.

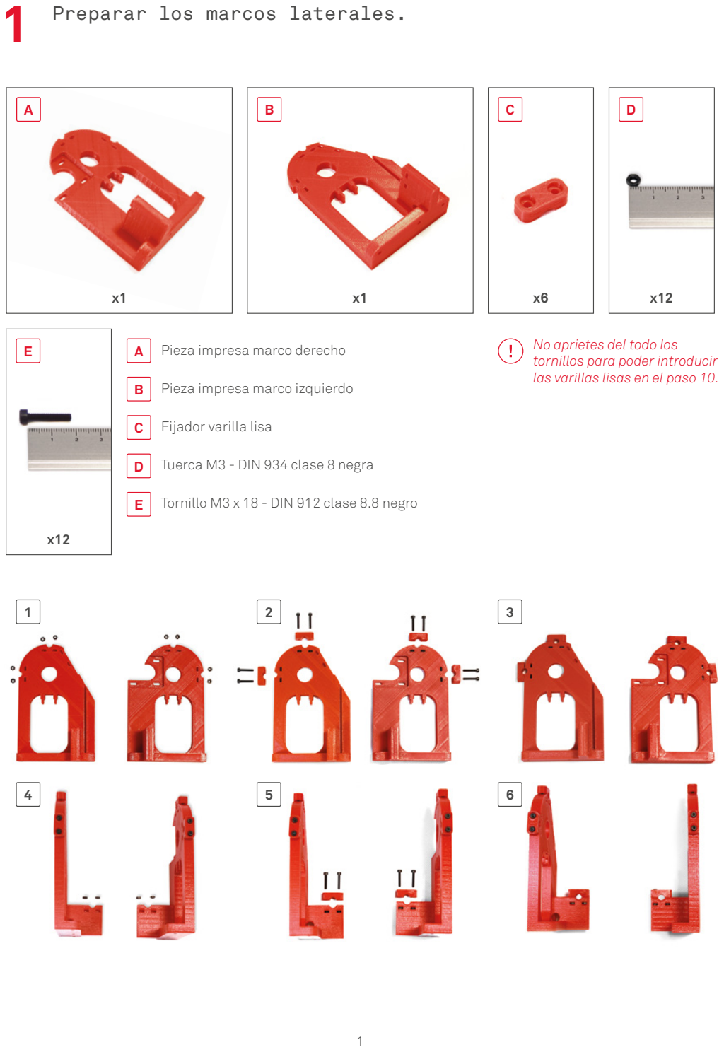
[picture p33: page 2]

x1 | x1 | x6 | x12

x12

A | B | C | D

E A

C

B

D

E

No aprietes del todo los
tornillos para poder introducir las varillas lisas en el paso 10.

Pieza impresa marco derecho

Pieza impresa marco izquierdo

Fijador varilla lisa

Tuerca M3 - DIN 934 clase 8 negra

Tornillo M3 x 18 - DIN 912 clase 8.8 negro

1 2

4 5

3

6

2 Anclar el sensor final de carrera del Eje X.

x1 | x1 | x2
A | B | C

A

B

C

D

x2

D

Pieza impresa marco izquierdo

Final de carrera

Tornillo M3 x 10 - DIN 912 clase 8.8 negro

Tuerca M3 - DIN 934 clase 8 negra

1 2

3 Pegar los protectores a la base de metacrilato.

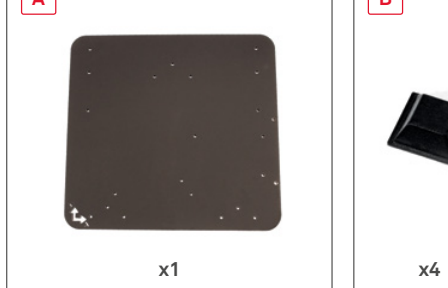
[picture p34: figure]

A | B | A
| | B

Montaje
Pega los 4 protectores de goma a la base de metacrilato. Toma como referencia el sistema de coordenadas de la esquina inferior.

Base de metacrilato

Protectores de la base de metacrilato

Despega la lámina protectora superior e inferior del metacrilato.

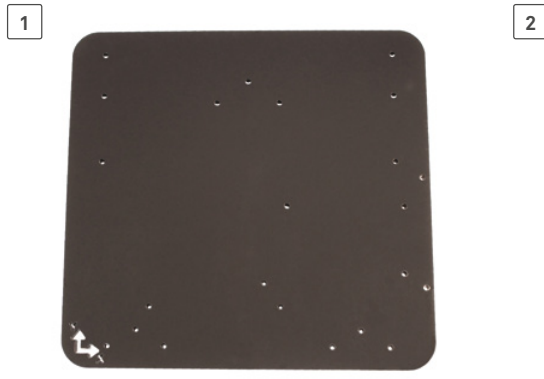
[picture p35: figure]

4 Fijar los marcos laterales.

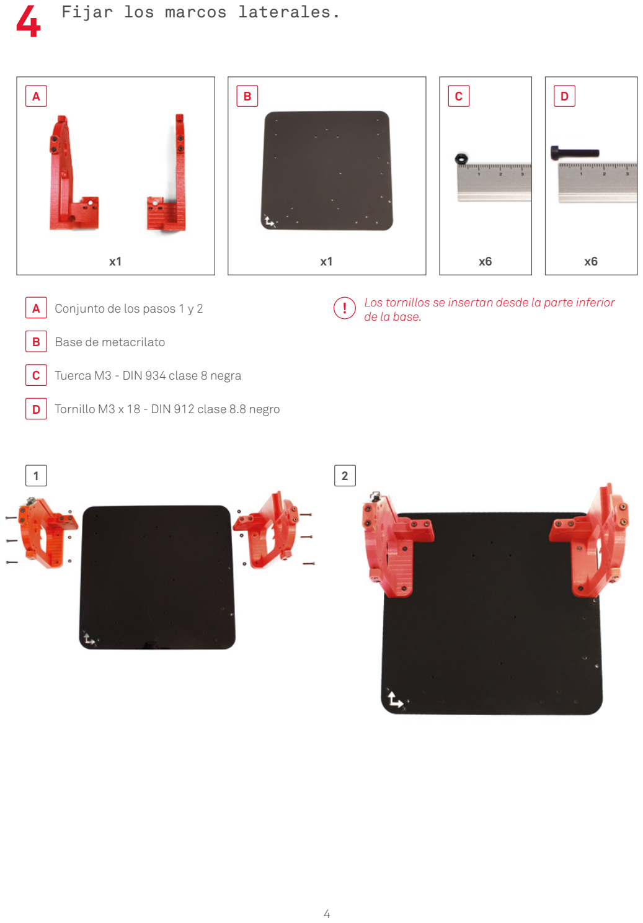
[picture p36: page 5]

x1 | x1 | x6 | x6
A | B | C | D

A

C

B

D

Conjunto de los pasos 1 y 2

Base de metacrilato

Tuerca M3 - DIN 934 clase 8 negra

Tornillo M3 x 18 - DIN 912 clase 8.8 negro

1 2

Los tornillos se insertan desde la parte inferior de la base.

5 Montar el final de carrera en el marco trasero.

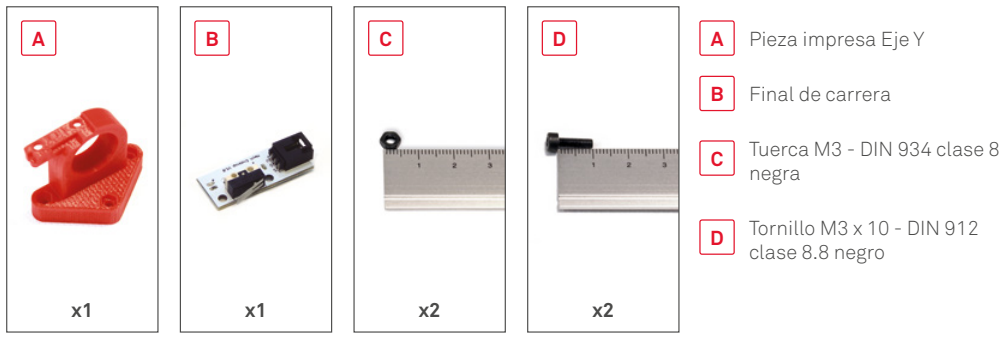
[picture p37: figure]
Pieza impresa Eje Y; Final de carrera; Tuerca M3 - DIN 934 clase 8 negra; Tornillo M3 x 10 - DIN 912 clase 8.8 negro
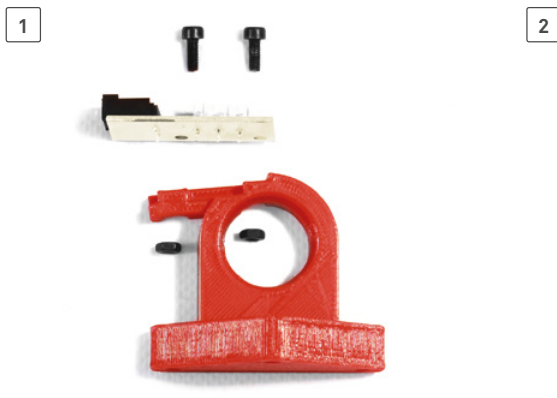
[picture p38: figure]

6 Fijar el marco trasero.

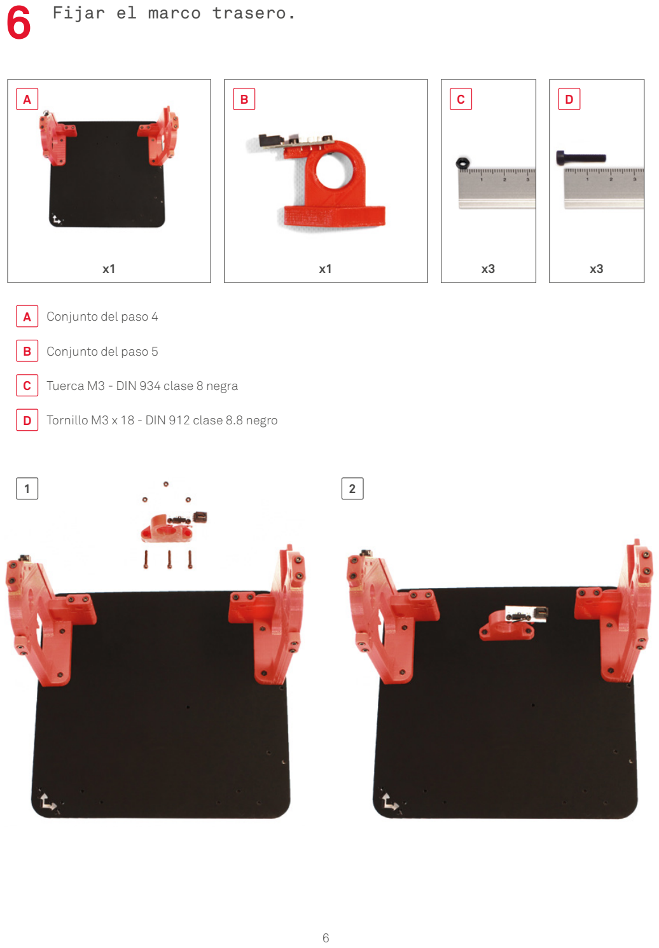
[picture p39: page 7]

x1 | x1 | x3 | x3
A | B | C | D

A

C

B

D

Conjunto del paso 4

Conjunto del paso 5

Tuerca M3 - DIN 934 clase 8 negra

Tornillo M3 x 18 - DIN 912 clase 8.8 negro

1 2

7 Fijar el marco frontal.

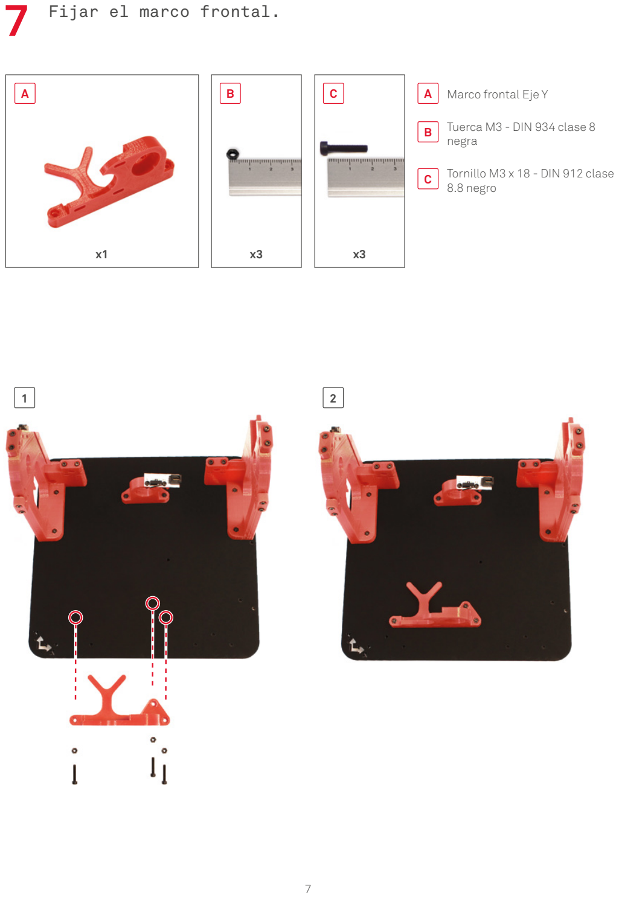
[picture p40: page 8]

1

x1 | x3 | x3
A | B | C | A

C

B

Marco frontal Eje Y

Tuerca M3 - DIN 934 clase 8 negra

Tornillo M3 x 18 - DIN 912 clase 8.8 negro

2

8 Fijar los soportes frontales.

x1 | x1 | x6 | x6

A

A

C

B

D

Soporte frontal izquierdo Eje Y

Soporte frontal derecho Eje Y

Tuerca M3 - DIN 934 clase 8 negra

Tornillo M3 x 18 - DIN 912 clase 8.8 negro

1 2

B | C | D

9 Preparar el soporte de los rodamientos lineales.

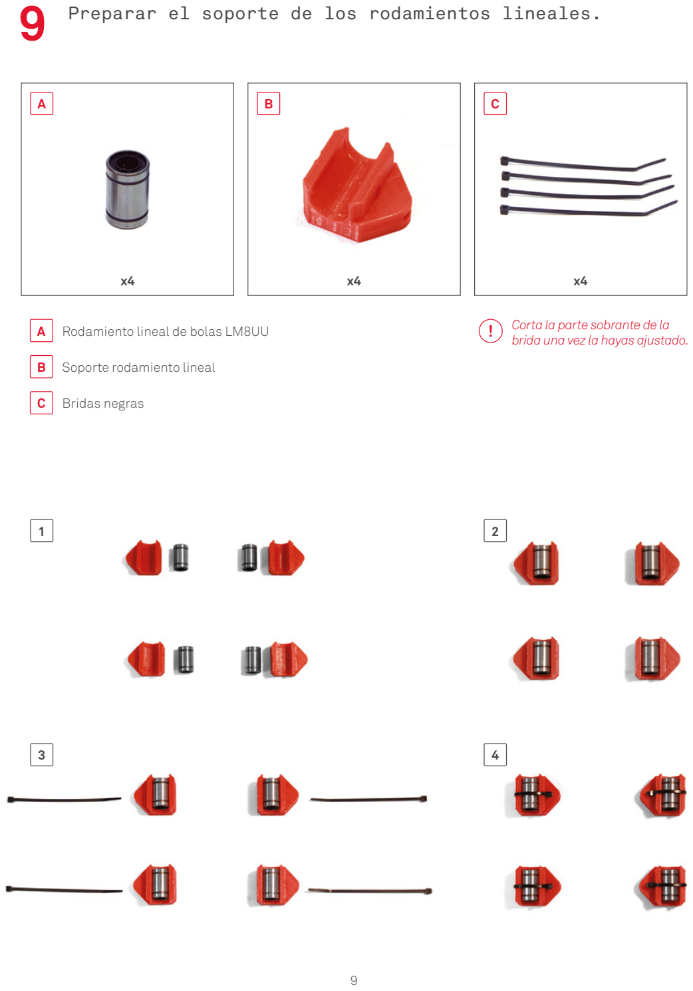
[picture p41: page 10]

Corta la parte sobrante de la brida una vez la hayas ajustado.

x4 | x4 | x4
A | B | C

A

B

C

Rodamiento lineal de bolas LM8UU

Soporte rodamiento lineal

Bridas negras

1 2

3 4

10 Introducir las varillas lisas en los rodamientos.

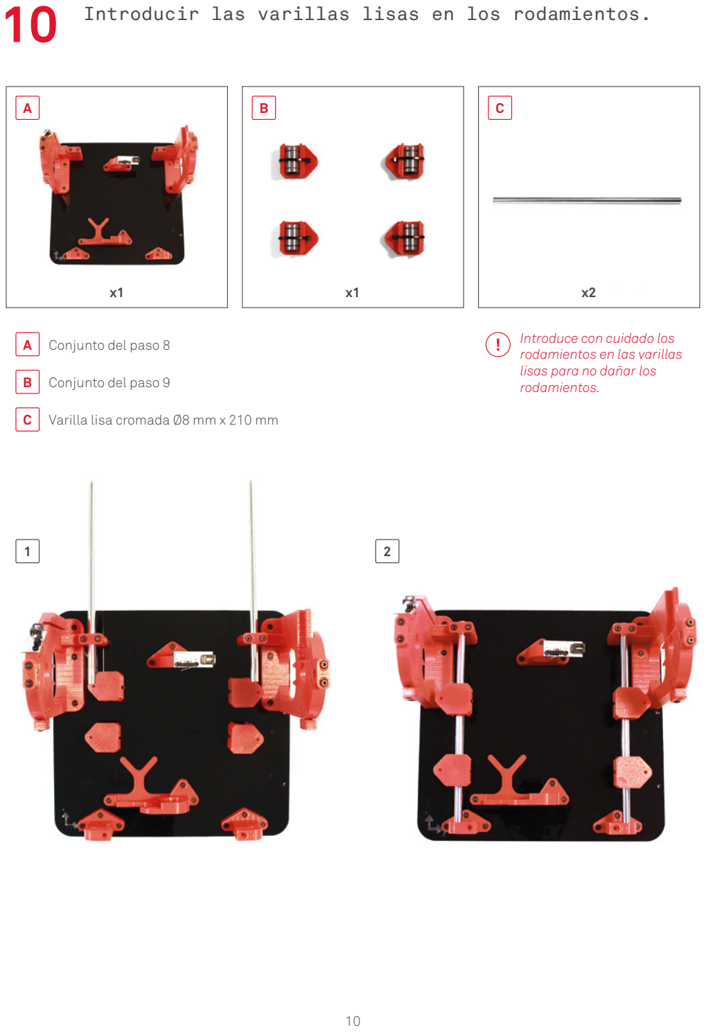
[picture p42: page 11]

Introduce con cuidado los
rodamientos en las varillas lisas para no dañar los
rodamientos.
x1 | x1 | x2
A | B | C

A

B

C

Conjunto del paso 8

Conjunto del paso 9

Varilla lisa cromada Ø8 mm x 210 mm

1 2

11 Fijar las varillas lisas.

x2 | x2
A | B | A
| | B

Tuerca M3 - DIN 934 clase 8 negra

Tornillo M3 x 18 - DIN 912 clase 8.8 negro

1

2

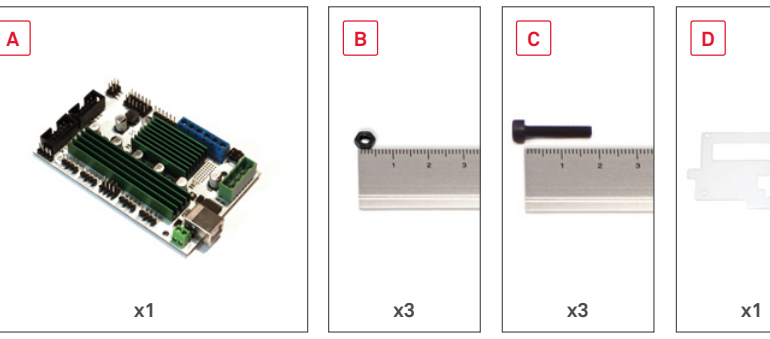
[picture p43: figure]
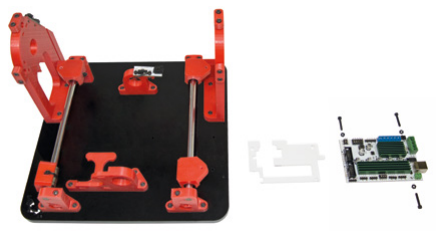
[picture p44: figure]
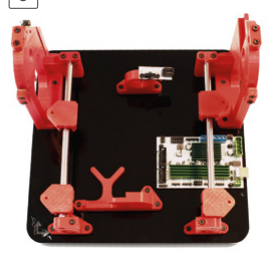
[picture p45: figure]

3

A

C

B

D

Montaje
Despega la lámina protectora del suplemento de electrónca, introduce los tornillos desde la parte inferior de la placa hacia arriba y fíjalos con las tuercas.

12 Acoplar la electrónica.

Placa Mega 3D

Tuerca M3 - DIN 934 clase 8 negra

Tornillo M3 x 18 - DIN 912 clase 8.8 negro

Suplemento de electrónica

2

1

Aprieta las tuercas ayudándote de la llave fija mientras sujetas el engranaje.

El lado en el que está embutida la tuerca debe quedar hacia la parte larga de la varilla.

13 Preparar la varilla roscada.

Muelle de 11 mm de diámetro y 15 mm de largo con 5 espiras

Montaje
La tuerca exterior debe quedar a ras de la varilla.

14 Acoplar la varilla roscada.

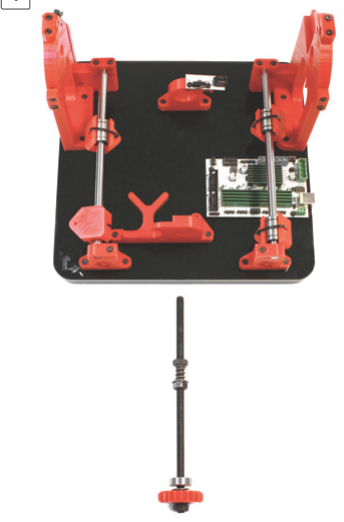
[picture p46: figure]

1

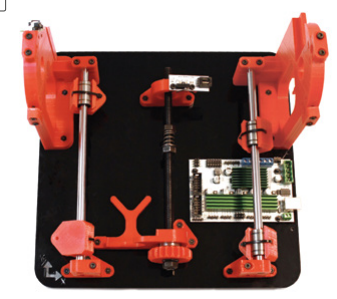
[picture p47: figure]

2

x1 | x1 | x1 | x1
A | B | C | D

A

C

B

D

Conjunto del paso 13

Tuerca M8 autoblocante

Muelle de 11 mm de diámetro y 15 mm de largo con 5 espiras

Rodamiento axial de bolas B608zz

Aprieta la tuerca autoblocante con una llave fija mientras sujetas con la mano el engranaje. La tuerca autoblocante debe quedar a ras de la varilla.
Fíjate en la posición de la tuerca autoblocante.

3

4

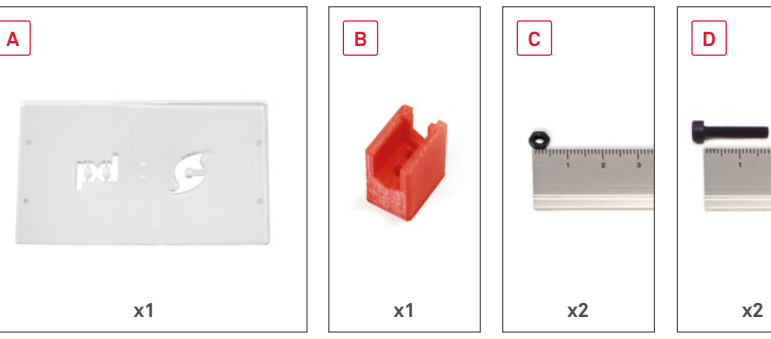
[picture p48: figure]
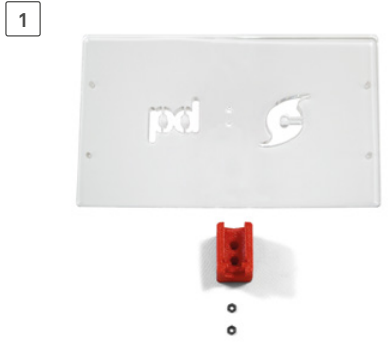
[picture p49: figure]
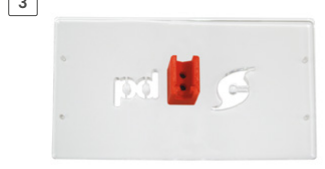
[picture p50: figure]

2

Fíjate en el logo de BQ para orientar la plancha de metacrilato. Es muy importante la orientación de la pieza impresa y del metacrilato.

A

C

B

D

15 Preparar la base de trabajo.

Base Eje Y de metacrilato 8 mm

Pieza impresa anti backlash Eje Y

Tuerca M3 - DIN 934 clase 8 negra

Tornillo M3 x 18 - DIN 912 clase 8.8 negro

3

Despega la lámina protectora superior e inferior del metacrilato.

16 Montar base y ajustar mecanismo anti backlash.

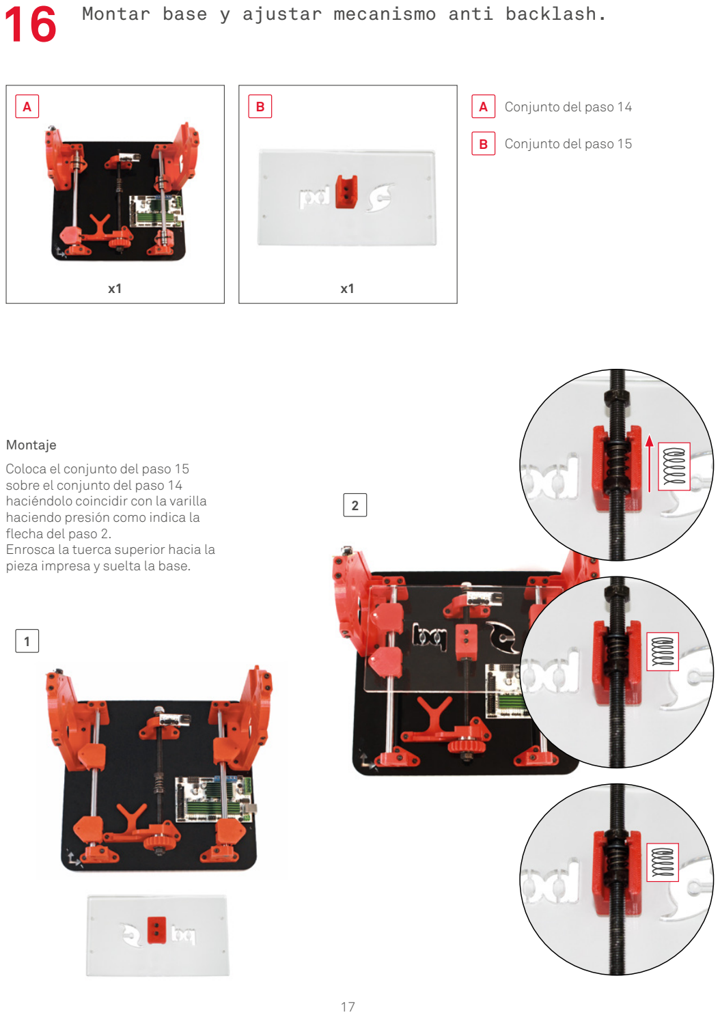
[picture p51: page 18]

1

2

x1 | x1
A | B | A
| | B

Conjunto del paso 14

Conjunto del paso 15

Montaje
Coloca el conjunto del paso 15 sobre el conjunto del paso 14 haciéndolo coincidir con la varilla haciendo presión como indica la flecha del paso 2.
Enrosca la tuerca superior hacia la pieza impresa y suelta la base.

17 Montar el soporte para la PCB.

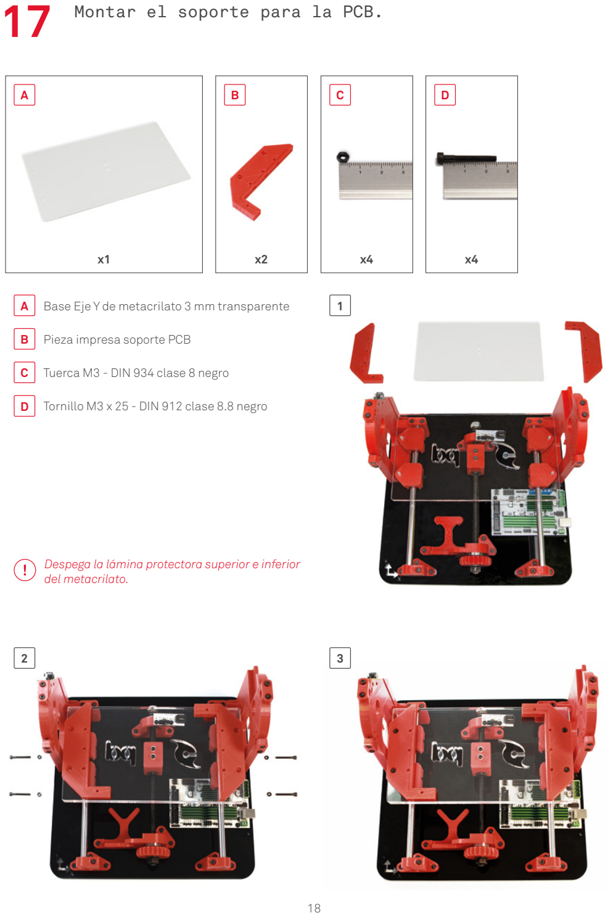
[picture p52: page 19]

1

2

x1 | x2 | x4 | x4
A | B | C | D

A

C

B

D

Base Eje Y de metacrilato 3 mm transparente

Pieza impresa soporte PCB

Tuerca M3 - DIN 934 clase 8 negro

Tornillo M3 x 25 - DIN 912 clase 8.8 negro

3

Despega la lámina protectora superior e inferior del metacrilato.

1 2

Aprieta el espárrago contra la parte plana del eje

D
Espárrago M3 x 4 - ISO 4026/DIN 913

18 Preparar el motor del Eje Y.

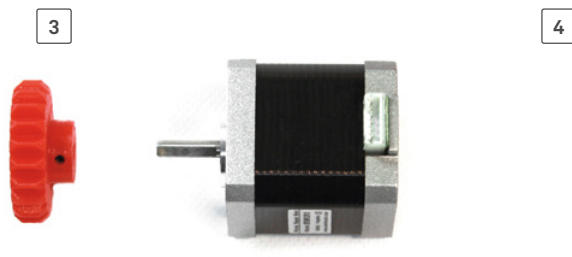
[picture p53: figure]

19 Montar el motor del Eje Y.

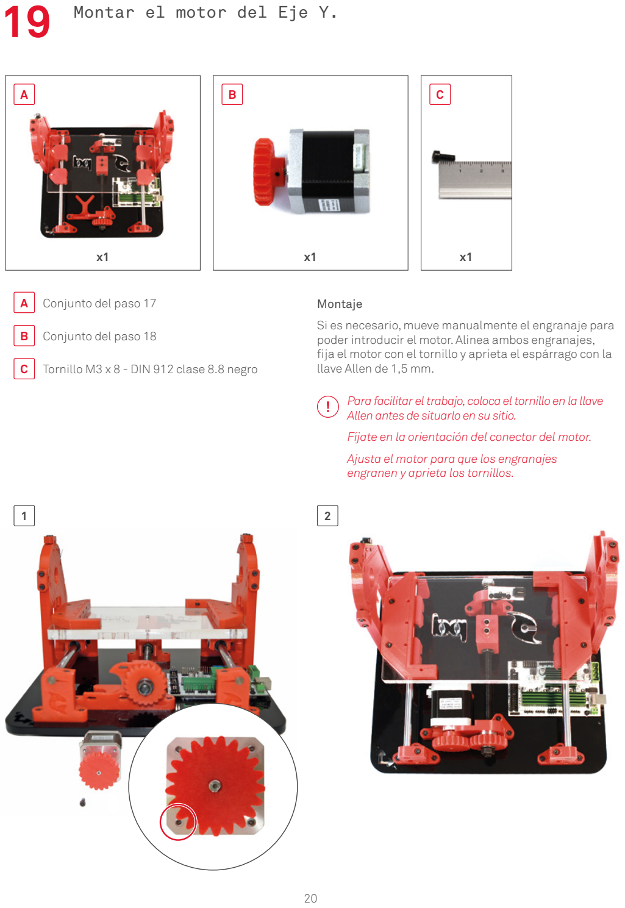
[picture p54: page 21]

Montaje
Si es necesario, mueve manualmente el engranaje para poder introducir el motor. Alinea ambos engranajes, fija el motor con el tornillo y aprieta el espárrago con la llave Allen de 1,5 mm.
x1 | x1 | x1
A | B | C

A

B

C

Para facilitar el trabajo, coloca el tornillo en la llave Allen antes de situarlo en su sitio.
Fíjate en la orientación del conector del motor. Ajusta el motor para que los engranajes engranen y aprieta los tornillos.

Conjunto del paso 17

Conjunto del paso 18

Tornillo M3 x 8 - DIN 912 clase 8.8 negro

1 2

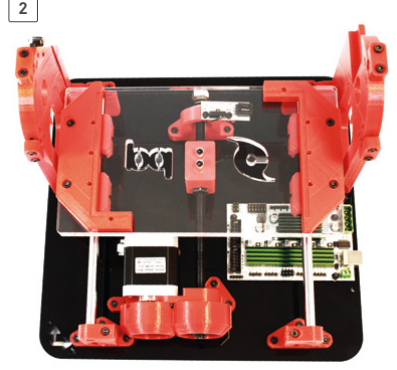
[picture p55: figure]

1 2

x1 | x2
A | B | A
| | B

20 Acoplar la tapa de los engranajes.

Pieza impresa tapa engranajes XY

Tornillo M3 x 10 - DIN 912 clase 8.8 negro

21 Anclar el soporte de la PCB parte B.

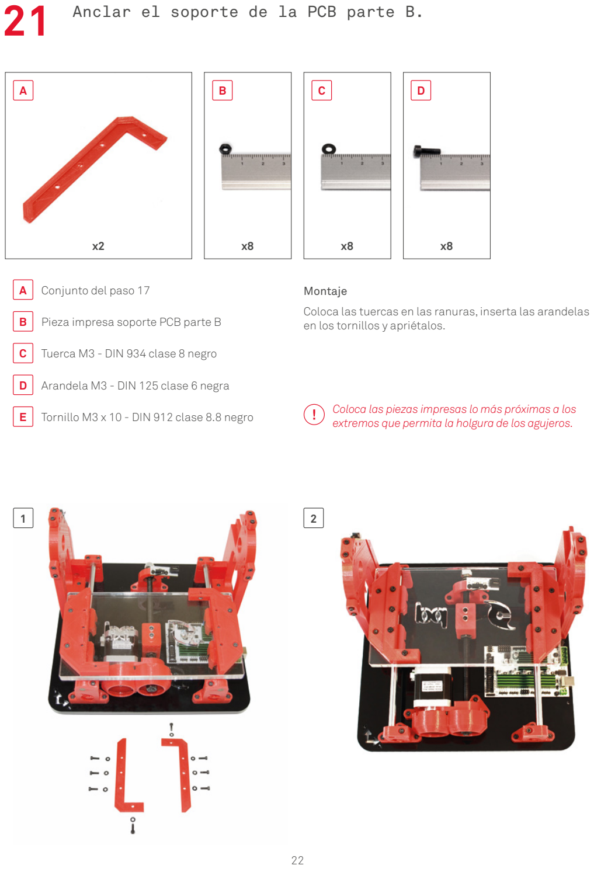
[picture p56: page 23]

x2 | x8 | x8 | x8
A | B | C

A

C

B

D

E

Montaje
Coloca las tuercas en las ranuras, inserta las arandelas en los tornillos y apriétalos.

Conjunto del paso 17

Pieza impresa soporte PCB parte B

Tuerca M3 - DIN 934 clase 8 negro

Arandela M3 - DIN 125 clase 6 negra

Tornillo M3 x 10 - DIN 912 clase 8.8 negro

1 2

Coloca las piezas impresas lo más próximas a los extremos que permita la holgura de los agujeros.

D

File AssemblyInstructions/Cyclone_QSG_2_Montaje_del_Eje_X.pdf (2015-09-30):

2

# Montaje del Eje X

### BQ Cyclone

1 Introducir las varillas lisas en el carro.

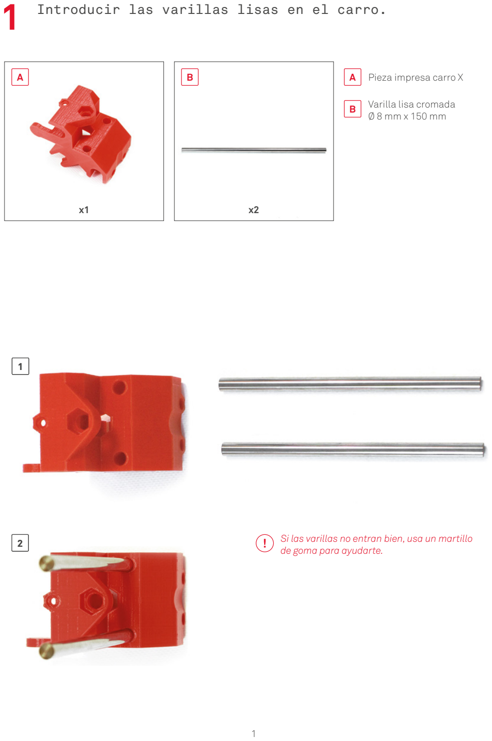
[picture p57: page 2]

A

B

x1 | x2

A B

1

### 2 Si las varillas no entran bien, usa un martillo

de goma para ayudarte.

Pieza impresa carro X

Varilla lisa cromada
Ø 8 mm x 150 mm

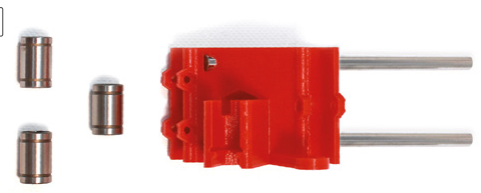
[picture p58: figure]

1

A

2 Introducir los rodamientos en el carro.

x3

A

Encaja los rodamientos en la pieza impresa asegurándote de que al hacerlo suena
un “click” y quedan bien
centrados.

Rodamiento lineal de bolas LM8UU

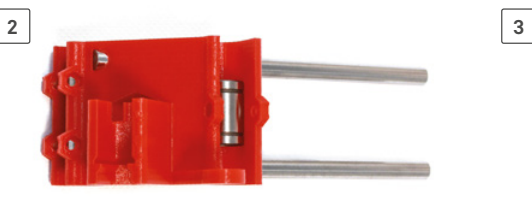
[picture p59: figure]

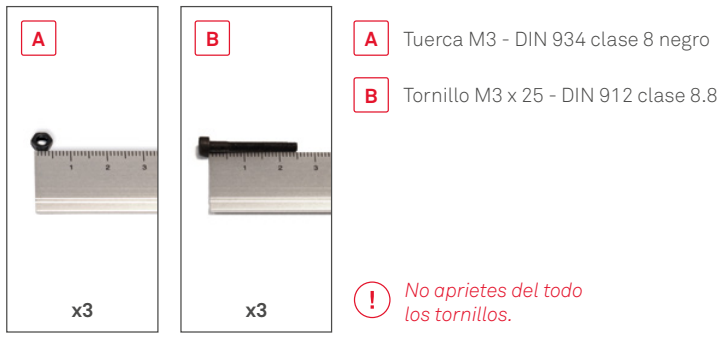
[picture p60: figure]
Tuerca M3 - DIN 934 clase 8 negro; No aprietes del todo; los tornillos.

Tornillo M3 x 25 - DIN 912 clase 8.8 negro

3 Sujetar los rodamientos del carro con tornillos.

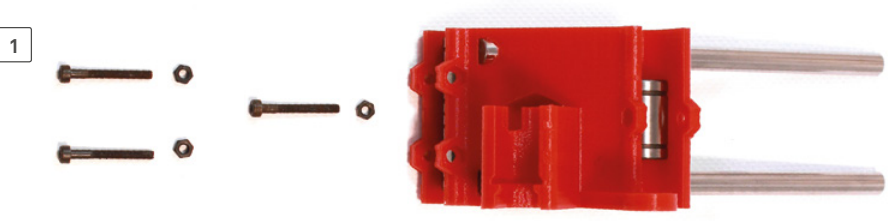
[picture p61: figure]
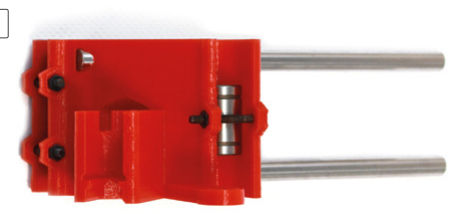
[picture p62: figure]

2

4 Preparar la varilla roscada.

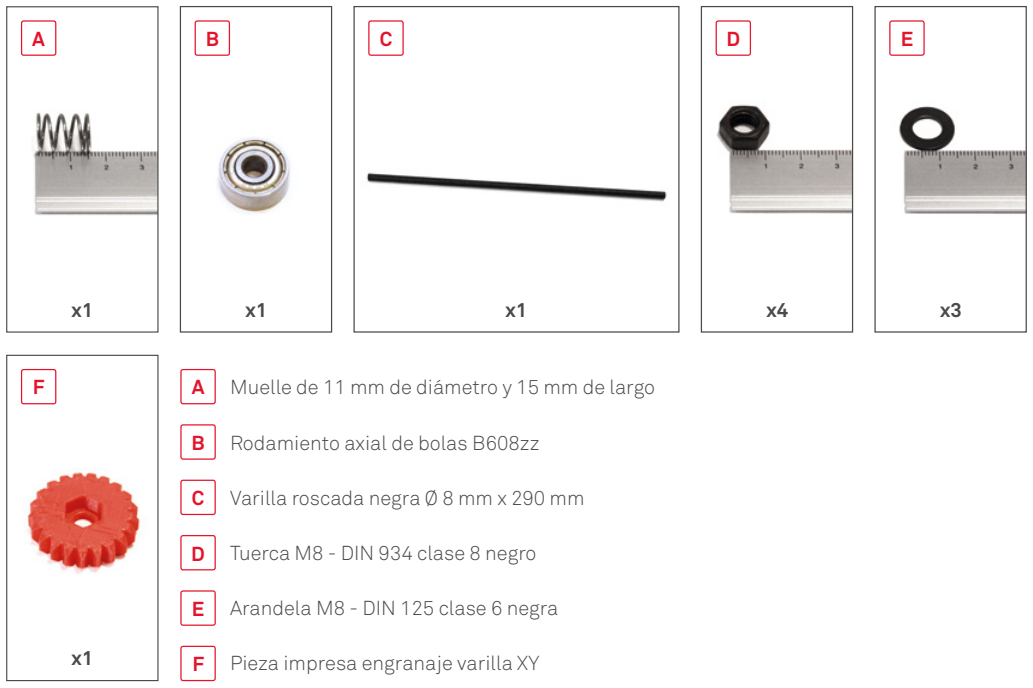
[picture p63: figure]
Rodamiento axial de bolas B608zz; Varilla roscada negra Ø 8 mm x 290 mm; Tuerca M8 - DIN 934 clase 8 negro; Arandela M8 - DIN 125 clase 6 negra; Pieza impresa engranaje varilla XY

Muelle de 11 mm de diámetro y 15 mm de largo

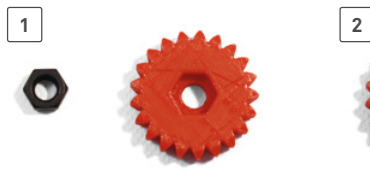
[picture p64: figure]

Aprieta las tuercas ayudándote de la llave fija mientras sujetas el engranaje.

El lado en el que está embutida la tuerca debe quedar hacia la parte larga de la varilla.

Montaje
La tuerca exterior debe quedar a ras de la varilla.

5 Introducir la varilla roscada.

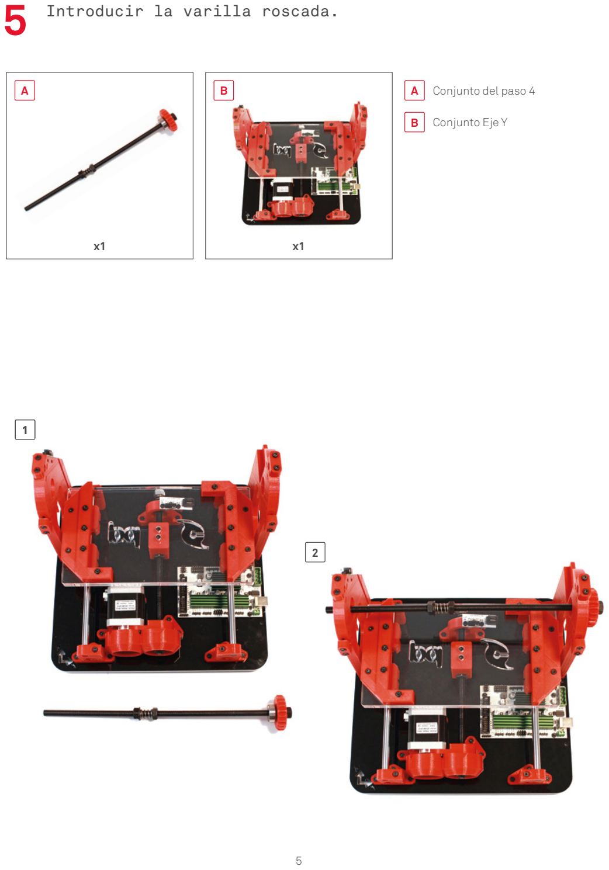
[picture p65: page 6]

A

B

x1 | x1
A | B | Conjunto del paso 4
| | Conjunto Eje Y

1

2

6 Montar el carro en las varillas.

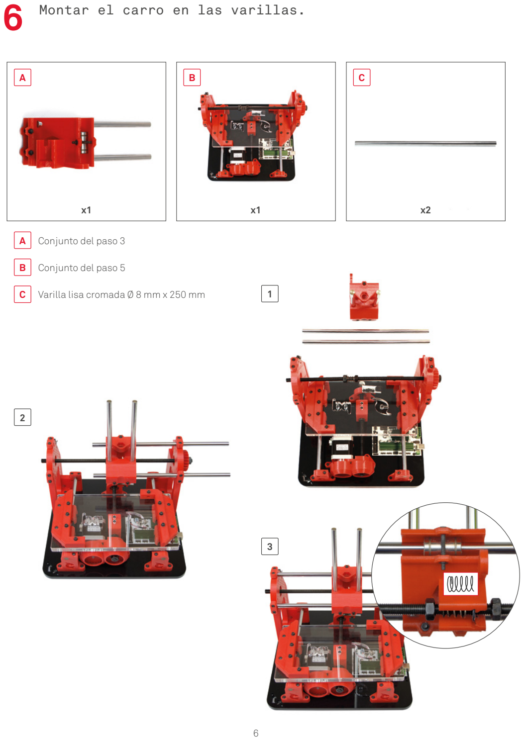
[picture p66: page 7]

A

B

C

x1 | x1 | x2
A | B | C

Conjunto del paso 3

Conjunto del paso 5

Varilla lisa cromada Ø 8 mm x 250 mm

2

1

3

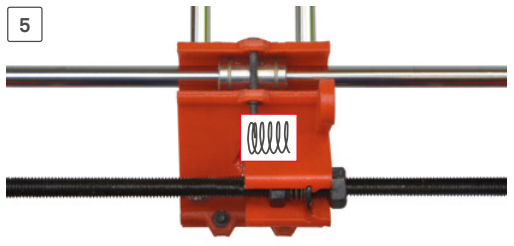
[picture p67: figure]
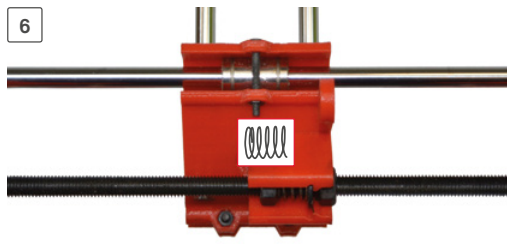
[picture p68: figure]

Montaje
Desplaza el carro según indica la flecha del paso 4 de forma que el muelle se contraiga.
Enrosca la tuerca derecha hacia la pieza impresa y suelta la varilla roscada.

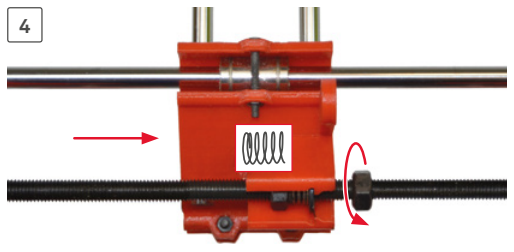
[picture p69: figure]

7 Apretar los fijadores de las varillas lisas.

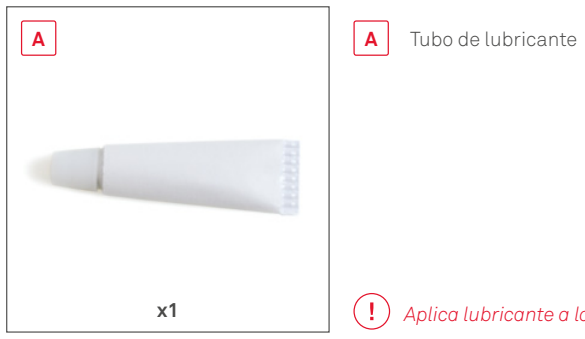
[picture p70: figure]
Tubo de lubricante

Aplica lubricante a las varillas roscadas.

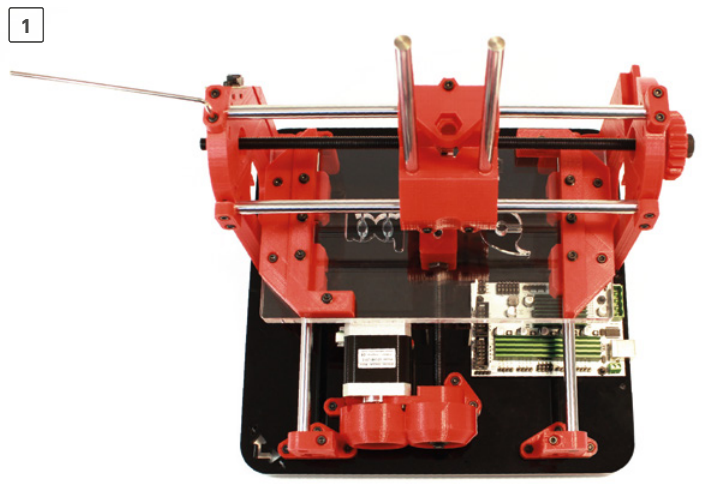
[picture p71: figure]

8 Montar el muelle del extremo de la varilla roscada.

Aprieta todos los tornillos que sujetan los rodamientos del carro.; Montaje; Rodamiento axial de bolas B608zz; Tuerca M8 autoblocante

Aprieta la tuerca con la ayuda de la llave fija sujetando el engranaje. La varilla roscada debe quedar a ras de la tuerca.

Muelle de 11 mm de diámetro y 15 mm de largo

Fíjate en la posición de la tuerca autoblocante.

9 Preparar el motor del Eje X.

No aprietes el espárrago del todo.; Motor Nema 17; Pieza impresa engranaje del motor XY

Aprieta el tornillo contra la parte plana del eje del motor.

C

D

Tuerca M3 - DIN 934 clase 8 negro

Espárrago M3 x 4 - ISO-4026/DIN 913


10 Acoplar el motor.


A

B

x1 | x1

A B

Ajusta el motor para que los engranajes engranen y aprieta el tornillo.
Asegúrate de que el conector del motor queda orientado hacia la parte exterior.

Conjunto del paso 8

Tornillo M3 x 8 - DIN 912 clase 8.8 negro

1

2

Montaje
Alinea ambos engranajes, fija el motor con el tornillo y aprieta el espárrago con la llave Allen de 1,5 mm.

11 Acoplar la tapa de los engranajes.


A

B

Pieza impresa tapa engranajes XY

Tornillo M3 x 10 - DIN 912 clase 8.8 negro

x1 | x2

A B

1 2

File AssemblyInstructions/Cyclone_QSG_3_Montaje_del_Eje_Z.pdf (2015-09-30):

3

# Montaje del Eje Z

### BQ Cyclone

1 Introducir los rodamientos en el carro.


1

3

x1 | x1 | x1 | x4
A | B | C | D

A

C

B

D

Pieza impresa inferior Eje Z

Pieza impresa superior Eje Z

Rodamiento axial de bolas B608zz

Rodamiento lineal de bolas LM8UU

4

2

2 Preparar la varilla roscada.


Usa la llave fija para apretar bien las tuercas. La tuerca embutida en el engranaje debe quedar hacia el extremo corto de la varilla.

Pieza impresa engranaje varilla Eje Z

Varilla roscada negra M8 x 95 mm

Tuerca M8 - DIN 934 clase 8 negro


3 Preparar el motor del Eje Z.

plana del motor.; Pieza impresa enganaje motor Eje Z; Motor Nema 17; Tuerca M3 - DIN 934 clase 8 negro

No aprietes del todo el espárrago contra la parte


D

Espárrago M3 x 4 - ISO 4026/DIN 913


4 Atornillar los tornillos de la abrazadera del carro.


1

3

x1 | x2 | x2 | No aprietes del todo los tornillos.
A | B | C | A
| | | B
| | | C

Conjunto del paso 1

Tuerca M3 - DIN 934 clase 8 negro

Tornillo M3 x 25 - DIN 912 clase 8.8 negro

2

4

5 Atornillar el motor a la parte superior del carro.


No aprietes del todo los tornillos.
Fíjate en la orientación del conector del motor.

1

2 3

x1 | x1 | x4
A | B | C

A

B

C

Conjunto del paso 3

Conjunto del paso 4

Tornillo M3 x 8 - DIN 912 clase 8.8 negro

6 Encajar la parte inferior del carro.


1

x1 | x1

A A

B

Conjunto del paso 4

Conjunto Eje X e Y

Montaje
Introduce con cuidado los
rodamientos en las varillas lisas.

2

B

7 Encajar la varilla roscada.


x1

A A Conjunto del paso 2

2

1

8 Encajar la parte superior.


1

x1

A

A Conjunto del paso 5

2

Los engranajes deben quedar alineados. Después, aprieta el espárrago del motor con la llave Allen de 1,5 mm y los tornillos que sujetan el motor con la llave Allen de 2,5 mm.

9 Insertar la herramienta rotativa.


La pestaña de la herramienta rotativa debe quedar apoyada en la pieza impresa.
Una vez colocada, aprieta las tuercas con ayuda de la llave 2,5.

Lee las advertencias de seguridad descritas en la Garantía y las instrucciones de uso de Dremel® 200 Series.

1

2

x1

A A Dremel® 200 Series

10 Preparar el acople para el aspirador.


1

3

x1 | x1 | x1
A | B | C

A

C

B

D

Pieza impresa tubo

Tubo de espirocristal 12 x 16 x 50 cm

Tuerca M3 - DIN 934 clase 8 negro

Tornillo M3 x 18 - DIN 912 clase 8.8 negro

2

4

Para usar Cyclone es aconsejable el uso de un aspirador.
Una vez introducido el tubo, aprieta el tornillo con la llave Allen.

x1

D

11 Preparar el adaptador para el aspirador.


Acoplar el adaptador al tubo.

1

x1 | x2 | x2
A | B | C | A
| | | B
| | | C

Pieza impresa acople

Tuerca M3 - DIN 934 clase 8 negro

Tornillo M3 x 18 - DIN 912 clase 8.8 negro

2

1 2

## 12 Acoplar el tubo del aspirador y el adaptador

a la herramienta rotativa.


1

3

A

B

x1 | x1

A B

Montaje
Desenrosca el embellecedor del extremo de la herramienta rotativa y coloca el acople del aspirador en el lugar del embellecedor.

Conjunto del paso 12

Pieza impresa protector

4

2

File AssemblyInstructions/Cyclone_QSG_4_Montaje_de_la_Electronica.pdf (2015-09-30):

4

# Montaje de la Electrónica

### BQ Cyclone

1 Preparar el cable de la fuente.


1

3

x1 | x1 | x1
A | B | C

A

B

C Conecta el cable rojo con la clema con el símbolo ‘ + ‘ y el cable negro con la clema con el símbolo ‘ - ‘.

Adaptador/conector Jack
Adaptador/conector Jack 2,1 mm hembra y Ramps 1.4 con clema de dos terminales.

Fuente 220 AC 12 DC 100W
Fuente con cable de 1,10 m, 100 W con conector Jack 2,1 mm (INPUT: 100-240V AC 1,8A 50-60Hz y OUTPUT: 12V DC 8.0A).

150 mm de cable flexible de dos hilos bicolor con sección de 1 mm²

2

4

2 Preparar los cables de los motores (opcional).

en ambos extremos; Tubo termoretráctil 50 cm; Soldador y estaño (no incluidos)

Montaje
Corta los cables e introduce un segmento de tubo termoretráctil de 2 cm por cada cable de motor. Después, suelda cada cable según la medida que se indica en la tabla.
Motor | Longitud (cm)
Y | 20
X | 30
Z | 60

Motor Nema 17 con conector macho 4 pines

Cable de cuatro hilos de 1 m de longitud con conector hembra 4 pines


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
## 3 Introducir los cables por el tubo recogecables

(opcional).

Quema los extremos del tubo para evitar que se deshilache.; Tubo recogecables 1 m; Bridas negras; Cable final de carrera 20 cm; Cable final de carrera 40 cm; Cables del motor

Montaje
Si has preparado los cables como se indica en el paso 2, corta el tubo recogecables según las medidas indicadas en la tabla e introduce los cables como se indica en las imágenes.
Tramo | Longitud (cm)
Motor Eje Z con el Eje X | 32
Motor del Eje X con el final de carrera
del Eje Y | 12

Final de carrera del Eje Y con la
Mega3D | 10

Final de carrera del Eje X con el motor
del Eje Y | 15
Motor del Eje Y con la placa Mega3D | 15


Final de carrera del Eje X con el motor del Eje Y

Motor del Eje Y con
la placa Mega 3D

Motor Eje X con el final
de carrera del Eje Y

Final de carrera del Eje Y con la Mega 3D

5

Motor Eje Z
con el Eje X

Coloca una brida en
cada extremo del tubo
recogecables.

4 Diagrama de conexionado de la placa.


Pon atención, ya que una mala conexión de los conectores de los finales de carrera puede dañar la placa.

En los conectores de los motores, fíjate en
la orientación del cable negro a la hora de conectarlos a la placa. El color del resto de los cables puede variar.

Montaje
Asegúrate de seguir el modelo de la imagen superior al realizar el conexionado. Presta atención al conectar los finales de carrera, debes conectarlos en la ristra de pines correspondiente indicados con la letra de cada eje. Los pines libres sirven para marcar el límite máximo de cada eje. En esta máquina no es necesario incluirlos, ya que este límite viene programado en el firmware.

5 Guiar cables.


Introduce el conector del
cable del final de carrera por
el orificio de la base, guíalo
por la ranura y conéctalo.

Final de carrera del Eje X con
el motor del Eje Y-Motor del
Eje Y con la placa Mega 3D

Motor Eje Z con el Eje X

el motor del Eje Y

Motor Eje X con el final de
carrera del Eje Y-Final de
carrera del Eje Y con la Mega 3D

Motor eje Z con el Eje X-Motor
Eje X con el final de carrera
del Eje Y

6 Atornillar la tapa de la electrónica.


x1 | x2 | x2
A | B | C | A
| | | B
| | | C

Pieza impresa tapa de la placa

Tuerca M3 - DIN 934 clase 8 negro

Tornillo M3 x 18 - DIN 912 clase 8.8 negro

1

2

Para realizar este paso, retira previamente el conector de la fuente de alimentación.
Los tornillos se insertan desde la parte inferior de la base.


Ya has terminado con el montaje de tu Cyclone.

### Antes de empezar a fresar, lee las indicaciones de seguridad descritas en la Garantía y visita:

### http://diwo.bq.com/product/cyclone

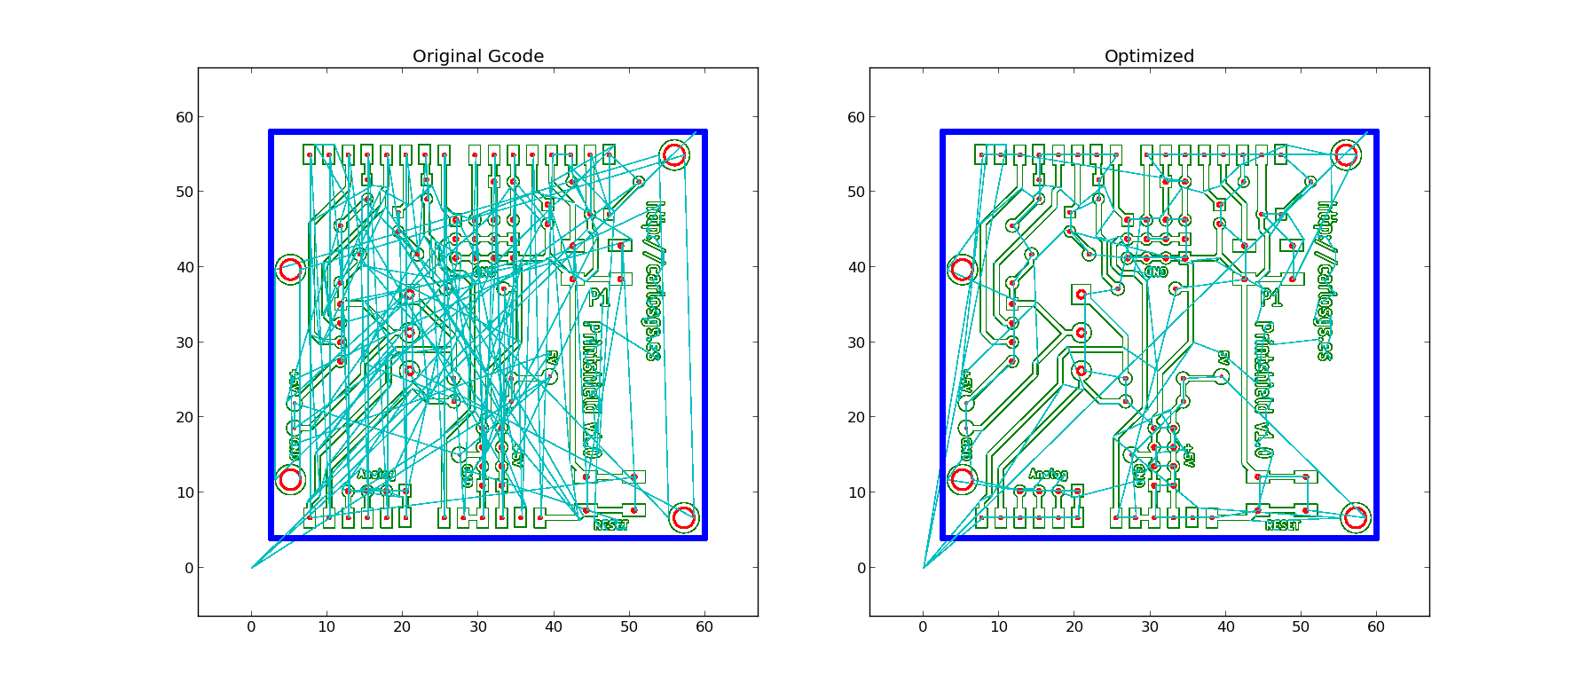
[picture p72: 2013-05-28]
Software/PythonScripts/Images/Printshield_optimization.png

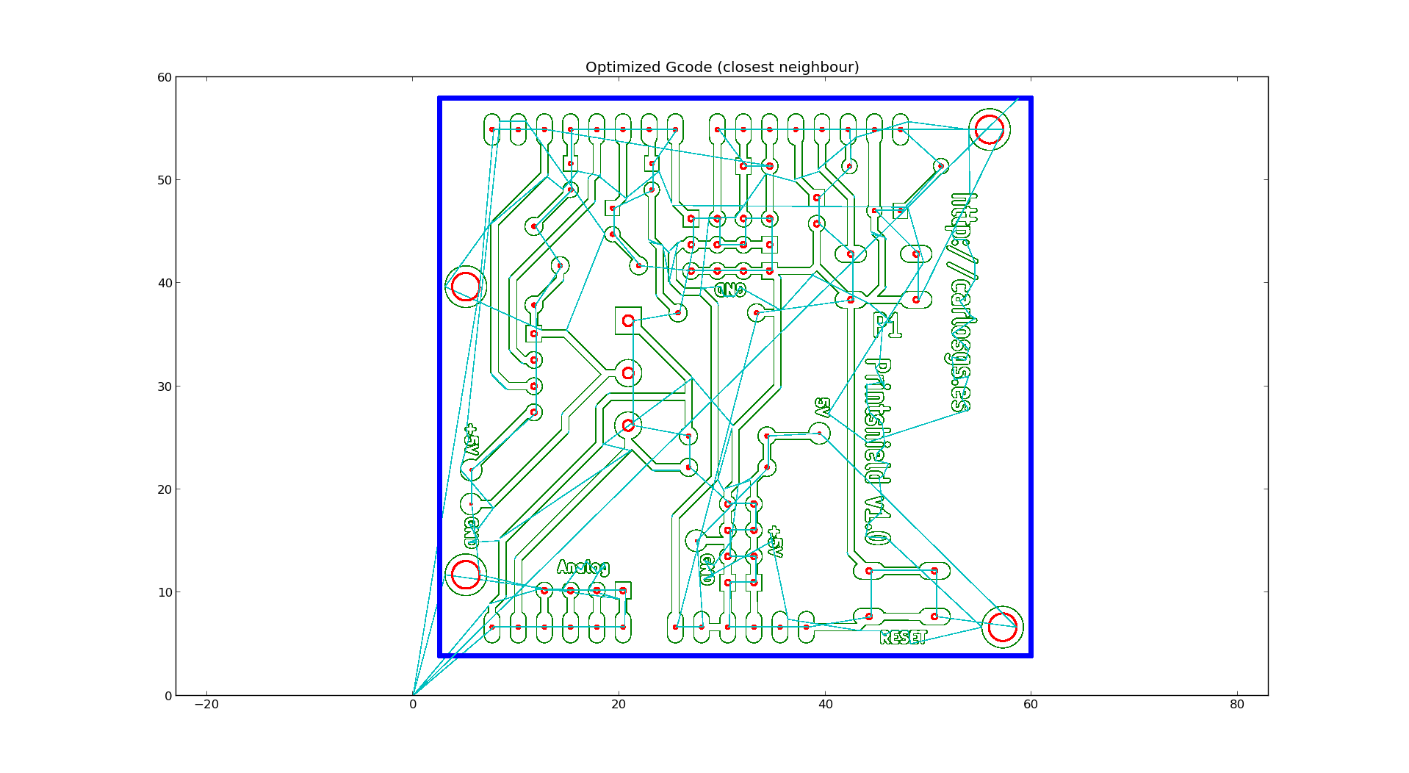
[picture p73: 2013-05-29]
Software/PythonScripts/Images/Printshield.png

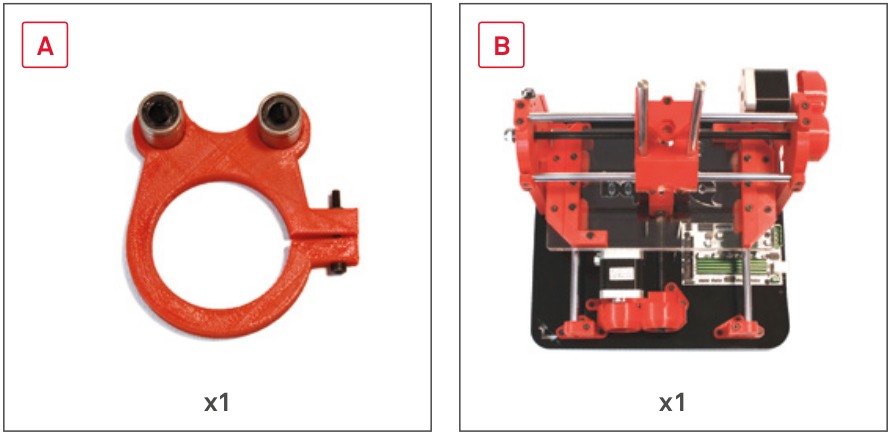
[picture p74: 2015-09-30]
AssemblyInstructions/3_Z_axis/6a.jpg

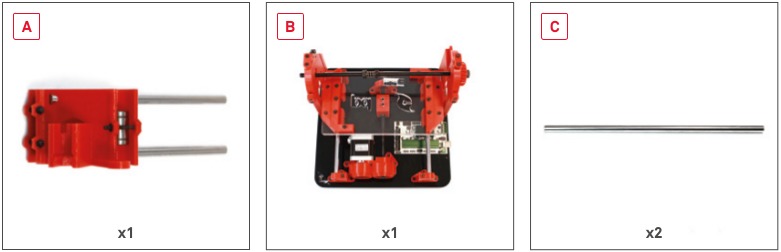
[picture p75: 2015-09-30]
AssemblyInstructions/2_X_axis/6a.jpg

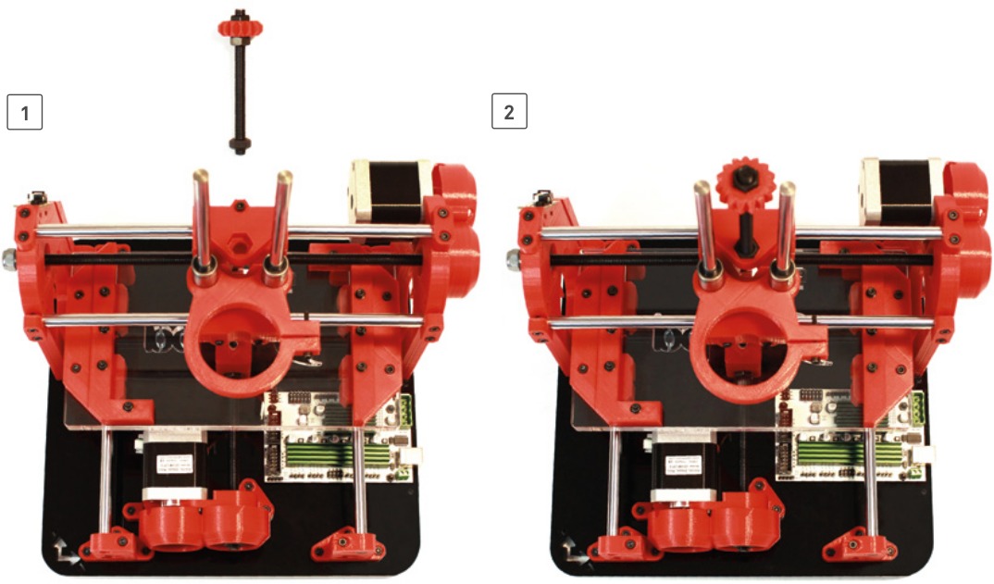
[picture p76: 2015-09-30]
AssemblyInstructions/3_Z_axis/7b.jpg

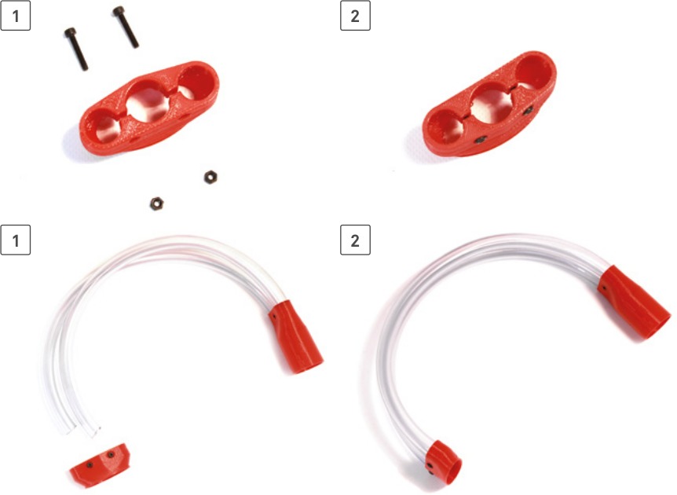
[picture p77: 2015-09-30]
AssemblyInstructions/3_Z_axis/11b.jpg

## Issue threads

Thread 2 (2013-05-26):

3 or 4 linear bearings to support the bed?

yOPERO, 2013-05-26:
Carlos,

The milling bed has currently 4  linear bearings supporting it and as the milling bed will be moving on a plane   (y axis), is it not more convenient to have 3 linear bearings which will give more stability in the case of pressure on the bed(drilling holes, Height probing,etc?

cheers.
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

Closed 2015-09-14.

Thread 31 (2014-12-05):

idea for improvement

ve3sjk, 2014-12-05:
Looking at the smooth rod holders seem to me like extra parts in a way. Would it not be easier to make the holes for the x smooth rods full holes and incorporate some captive nuts going into the frame to hold them. something like the way the drive gears are held onto the motors. It would eliminate all the smooth rod holders, half the hardware, and possibly make things squarer. I find the pressure and how evenly you tighten the holders done, effects the squareness of the rods based on how good the half circle printed in the holders themselves.

 Just thinking out loud on this one,

carlosgs, 2015-09-14:
I think it makes sense to reduce hardware, but having "open" holders simplifies the assembly process quite a lot!

Closed 2015-09-14.

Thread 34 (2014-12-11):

endstop holders

ve3sjk, 2014-12-11:
I have modified my files a bit to allow for different end stop configurations, so far i moved the end stop out of the standard parts lib, added as a separate scad file and included it in the main scad file. I moved the parameters for it to the configuration files and added if statements to suppress it in the x-frames files. I have this machine setup to offset the x axis to the middle so i am running an offset of -180 instead of -80 for that setting. I am working off a base files that are v2.1.

Everything is working except for this behavior, not sure where in the code i need to make changes to stop it.

the left frame without with end stop

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

and with it turned on

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

the right frames printed good, but i guess you could say the same for motor mount structure as well it just continues to the end of the frame although it doesn't bother me at all.

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

carlosgs, 2015-09-26:
Fixed with Cyclone XL <https://github.com/carlosgs/Cyclone-PCB-Factory/tree/master/Output_files/Cyclone_XL> :-)

Closed 2015-09-26.

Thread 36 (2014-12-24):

Changing Feed Rates in GCode not being honoured

joco-nz, 2014-12-24:
As part of the calibration of the CNC I wanted to use the zig-zag pattern from precisebits.com.
I created a fixed co-ord version so that it rendered nicely in gcode-cnc-controller and did a dry run (i.e. Z 0 set at 3mm above the copper).
The whole idea behind this code zig-zag is to change the feed rate on each line so that you can tune in what is the best feed rate for this material.   However the feed rate changes are NOT being honoured.

Anyone able to replicate this?

Code below incase I have an issue in that.  Note this version starts fast and slows down.  This was done to debug the issue and speed up the process.:
```
G90
G00
G21
F400
G01 Z15
G01 X0 Y0
M03
F60
G01 Z-0.1
G90
( **START ZIGZAG** )
F150
G01 X24 Y3
G01 X0 Y6
F130
G01 X24 Y9
G01 X0 Y12
F110
G01 X24 Y15
G01 X0 Y18
F90
G01 X24 Y21
G01 X0 Y24
F70
G01 X24 Y27
G01 X0 Y30
F50
G01 X24 Y33
G01 X0 Y36
F30
G01 X24 Y39
G01 X0 Y42
( **END ZIGZAG** )
G90
G00
F400
G01 Z15
G01 X0 Y0
M05
M02
```

joco-nz, 2015-01-04:
Closing as there is a working pattern identified by @ve3sjk .

Closed 2015-01-04.

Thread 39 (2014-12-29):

Motor gears not rendering properly

carlosgs, 2014-12-29:
I am not sure of the reason behind this rendering problem. It seems to happen only in the gears.

After pressing F5:
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

After pressing F6:
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

carlosgs, 2015-02-04:
This issue has been magically fixed. The most likely cause of this was the use of a nighly OpenScad build

Closed 2015-02-04.

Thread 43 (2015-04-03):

Guide

z3t0, 2015-04-03:
Hi,
I am very interested in this and would definitely like to contribute to the development. Could you please give me some pointers as to where to begin as I would love to build this first and understand (to some extent) how it works so I can help to my fullest ability.

Thank you to all the contributors for this amazing project! :smile:

carlosgs, 2015-04-09:
Hello, there is no build guide yet, but a good source to follow is Joco's thread in the mail list:
https://groups.google.com/forum/#!topic/cyclone-pcb-factory/o_YzXokpLnA
Also the mail list is the best place to check for guidelines :)
Good luck with your build!!

Cheers,
Carlos

PD: Will link it here when a build guide becomes available

Obijuan, 2015-04-09:
It will be very soon :-)

z3t0, 2015-04-09:
Sounds good, if you need any help let me know. I will get started on trying to build one and make sure to document the process. How much do you think the net cost will be? Excluding the price for the 3D printed parts?

carlosgs, 2015-04-12:
The cost depends on many factors, I find it difficult to give estimates.

If you already have 3D printer hardware/electronics that can be recycled for the project, it can be very cheap. Very roughly, sourcing all the parts should be under 250€ ~(cost of a 3D printer, minus {one motor, hotend, heating/sensing elements, LCD?, etc}, plus {dremel,springs}).

Again, depending a lot on the setup you want and the sources you use :-)

Cheers,
Carlos

z3t0, 2015-04-12:
@carlosgs Okay, in that case could you make some sort of materials list I can work off, because the one on the README.md is quite confusing. Thanks

carlosgs, 2015-09-14:
Here are a couple of guides:
BQ: http://diwo.bq.com/product/cyclone/
[PDFs with the instructions](http://diwo.bq.com/wp-content/uploads/2015/08/Manual_ES_pdf.zip)

Also you have the build manual by Tatubias: http://reprap.org/wiki/Cyclone_PCB_Factory_Build_Manual

Cheers,
Carlos

Closed 2015-09-14.

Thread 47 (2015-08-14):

Como hacer milling con Fritzing

b4zz4, 2015-08-14:
Tengo una cyclone-pcb desde hace unos meses y quería hacer un circuito usando fritzing por que el resto de los programas me resultan complicado y no los uso muy bien, ¿existe algún tutorial de como hacer esto?

saludos

carlosgs, 2015-08-17:
Hola, pregúntalo en el foro español (https://groups.google.com/forum/#!forum/cyclone-pcb-factory-es ) o inglés (https://groups.google.com/forum/#!forum/cyclone-pcb-factory ).

No he usado Frizting pero imagino que puede exportar como Gerber; una vez tengas los ficheros Gerber, puedes usar el programa FlatCam (http://flatcam.org/manual/index.html ) para generar los Gcode.
Saludos,
Carlos

Closed 2015-08-17.

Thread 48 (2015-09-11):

XY gear cover

PaulusJB, 2015-09-11:
Hi,
I'm having a bit trouble with "Cycl_XYgearCover_x2.stl", even with "Cycl_tapaEngranajesXY.stl" which remains as the same file; stl's broken!
any possibility of reuploading a new export?

carlosgs, 2015-09-11:
Hi Paulus, which software are you opening them with? They work fine with Cura. May I suggest opening them with Cura and saving into a new STL file?

PaulusJB, 2015-09-14:
I was trying to make a .gcode using slic3r, and for some reason it shows it broken-like. Using Cura was the solution!

carlosgs, 2015-09-14:
Awesome, thanks for getting back to confirm it! :D

Closed 2015-09-14.

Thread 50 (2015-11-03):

consulta sobre engranajes

b4zz4, 2015-11-03:
¿probaron usar engranajes estilo [Herringbone](http://reprap.org/wiki/Herringbone_Extruder_Driver) ?

carlosgs, 2015-11-03:
Hola! Sí, la primera versión usaba ese tipo de engranajes:
<https://github.com/carlosgs/Cyclone-PCB-Factory/releases/tag/v0.9.7>

Al final decidí cambiarlos por engranajes normales debido a que si no se imprimen perfectamente, la estructura Herringbone "baila" un poco y transmite esa vibración en forma de movimientos axiales (es decir, hace oscilar la varilla roscada longitudinalmente).
Con engranajes normales, sigue siendo posible una cierta oscilación, pero ésta queda desacoplada.

Si te preocupa el backlash entre los dientes de los engranajes, piensa que la reducción con la varilla roscada es muy grande y minimiza dicho efecto.

Saludos,
Carlos

Closed 2015-11-03.

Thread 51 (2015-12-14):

Issues slicing models

kmckee, 2015-12-14:
I'm having a heck of a time getting Slic3r to slice a lot of these models.  I'm wondering what is recommended?

Also, if it makes sense I'd like to add this to the readme.

Thanks; I can't wait to get this built and running.  Very cool project!

kmckee, 2015-12-14:
So, I've been able to repair the models and then slice them successfully.  I did an automatic repair using the free version of Netfabb.

Should I send a pull request with the repaired models?

carlosgs, 2015-12-14:
Hi Kyle, I normally use Cura, which seems to incorporate the "auto repair
stl" feature, so I've never really had any problems slicing them.

But yeah it would be great to provide fixed STLs for people that uses
different gcode generators. I'd appreciate that pull request :-)

If it's not too much of a hassle, could you replace each STL in a separate
commit? That way it is easier for me to check for any difference. I'm a bit
worried the repair process may close screw holes.

On 14 Dec 2015 04:39, "Kyle McKee" <notifications@github.com> wrote:
>
> So, I've been able to repair the models and then slice them successfully.
I did an automatic repair using the free version of Netfabb.
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

kmckee, 2015-12-16:
Hi Carlos,

I have this all ready to go, but I don't think it's possible send a PR against the v2.2 tag.  When I switch the base from a branch to a tag, github removes the "Create Pull Request" button.

Everything is in my fork here:  https://github.com/kmckee/Cyclone-PCB-Factory

First, does it make sense to repair the v2.2 stls?  If so, can you create a branch on the v2.2 tag so that I can submit the PR?

carlosgs, 2015-12-16:
Hi, the merge is done :-)
With the following commands:
'''
git remote add kmckee git@github.com:kmckee/Cyclone-PCB-Factory.git
git fetch kmckee
git merge kmckee/repairs
'''
Github seems to be clever enough to re-locate the files that were moved to different folders.

Thanks so much for taking the time to fix all of the STLs, and for logging the changes with separate commits, it helped a lot!!

kmckee, 2015-12-16:
Awesome!

NP; thanks for all your work on this.  I'm eagerly waiting for parts in the mail so I can put it all together :)

Closed 2015-12-16.

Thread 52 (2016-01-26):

Question about gears

czapeczek, 2016-01-26:
Hi.

I just wanted to know (sorry if it's written somewhere - wasn't into docs really yet, I am trying to understand what I see here first) why the motors are connected to their axes with gears and  not directly?

Hope I'll hear an answer :)

Filip

Alexthefox, 2016-01-26:
Hi, I have print the same of original project. The reason is for torque of the motor. But somebody did it with direct drive, motor connect to threaded bar. Of course if change ratio of motor, need to'd change in firmware.

Alessandro

Inviato da BlueMail

Il giorno 26 gen 2016 19:42, alle ore 19:42, czapeczek <notifications@github.com> ha scritto:
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

czapeczek, 2016-01-26:
Okay, I assume, that by mounting a direct drive - the accuracy will be a lot better.

CarlosGS, 2016-01-26:
Gears were kept in place in order to reduce the size of the machine
Bear in mind that any backlash in the gears will be fed through the threaded rod, which is a very large reduction. You can actually have lots of backlash in the gear mechanism before it has any noticeable effect in quality

On the other hand, a word of advice. Threaded rods are usually not calibrated, which means they are not nearly as accurate as a proper industrial-grade leadscrew. If you are implementing direct drive for the sake of quality, I'd tell you to also replace the threaded rods for leadscrews

Also, please join us in the mail list: https://groups.google.com/group/cyclone-pcb-factory

Cheers,
Carlos

czapeczek, 2016-01-26:
Am joining right now :)
Thanks!
The first thing I was thinking of was to changer the throds to ldscrews

Closed 2016-01-26.

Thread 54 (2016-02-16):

Is the BoM actual?

czapeczek, 2016-02-16:
I printed all the parts. It seems 2 gears not fit the M8 threaded rod and even the motor head.
So either BoM is not actual or something is not to scale with this gears.

I mean here gears for Z axis.

veelck, 2016-02-16:
As far as I managed to check this issue, it seems that `Cycl_Z_carriage.scad` has a bug, where it has the  `cyclone_rod_gear` call - it uses tolerance=0, where in case of X and Y axis there is tolerance set to `screwHoleTolerance`.

As for the second gear, it seems like the diameter of stepper motor rod is hardcoded inside the `standard_parts.scad`, which seems strange as I'd expect it to be configured.
It also has tolerance=0, but modifying that sets the tolerance on both holes (the motor rod as well as screwing hole, which is not really ideal).

I'd love to issue a pull request, but I'm not sure if my changes will make sense, since I'm noob in scad (started to figuring it out like 2h ago ;))

I'd love to get some feedback before I'll issue the PR.

veelck, 2016-02-17:
I'd added the `tolerance = screwHoleTolerance` for both gears, printed them and it worked like a charm, so I guess that's the problem.

CarlosGS, 2016-02-17:
@veelck Thanks for the PR! Would you mind updating the STL with the gears as well?

Interestingly enough, most complains regarding the tolerances so far have pointed out they were too large. So maybe these gears were an exception because of the bug

Thanks to both for the bug report!

veelck, 2016-02-17:
@CarlosGS Hi, thanks for taking the PR.

Can you give me some tips on how to optimally generate the STLs? Like I mentioned, I'm new to OpenCAD and I'm not sure how can I make it so it makes sense (for the gears I needed I exported them one-by-one, so for all the gears that'd be pain in the a..., hope it's not the only way...)

CarlosGS, 2016-02-17:
Unfortunately that is the case, STLs need to be manually generated for every part. What I often do, is render an STL for the full machine, then load it in Cura and choose "split into parts", finally arrange the parts into the proper alignment for 3D printing

I agree, it is tedious. But if you still have around the updated STLs, what I'd do is load [the old gear plate](https://github.com/CarlosGS/Cyclone-PCB-Factory/blob/master/Output_files/Cycl_allGears.stl) in Cura, then choose "split into parts", remove the Z gears, then drop the new STLs into Cura, and finally save the new STL plate
Sorry for the inconvenience, it would be great to have a way to automate this, indeed

CarlosGS, 2017-02-25:
Merging this issue with #57

Closed 2017-02-25.

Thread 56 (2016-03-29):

Which parameters should I use to print the parts?

gsalvati, 2016-03-29:
**Which parameters should I use to print the parts?**
I found only this:
https://github.com/CarlosGS/Cyclone-PCB-Factory/tree/v2.3/Output_files/STL_plates

Can I use this configuration to print all the parts?

CarlosGS, 2016-03-30:
Indeed! Some people have reported that holes are too large when printing at very fine resolution, so in fact it is better to use the coarse settings

Maybe I'd raise a little bit the fill density, to 25%
Please let me know of any issues while printing the parts

gsalvati, 2016-03-31:
Thanks a lot

Closed 2016-03-31.

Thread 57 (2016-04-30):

Gears STL files have a wrong scale? - V2.3

GregLukosek, 2016-04-30:
Noticed 2.3 allGears.stl are too big. causing the excesive loose between gear and a m8 nut.
Video illustrating the issue https://www.dropbox.com/s/prcmcj2ue2snl6q/File_000.mov?dl=0

2.3 version have about 13.6mm nut space
2.0 version have about 13.3mm nut diameter

Both 2.3 and 2.0 are too big. M8 nut is about 12.9mm.
http://imgur.com/DZFrtAF

DKfraDK, 2016-06-21:
@GregLukosek did you solve this?

kaiwety789, 2016-08-06:
Leave a comment

kaiwety789, 2016-08-06:
Comment on issue

kaiwety789, 2016-08-06:
Desktop version

p2baron, 2016-08-25:
Also the hole for the stepper shafts is too big.
I notices that the holes for the M8 nuts and stepper shafts are only incorrect on the four bigger gears.

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

Is this fixed in the development repo?

lasicmk2, 2016-10-17:
have you checked printer calibration?
I hot the same issue but after checking all steps/mm everything is fine

p2baron, 2016-10-17:
Yes the printer was fully calibrated. (i3 mkII)
Solved this by editing the configuration for the Openscad model. l've decreased tolerances for the nuts, bearings and smoothrods. Now everything has a tight fit.

JohanBraeken, 2016-11-05:
I was bitten by this issue as well and believe, the tolerance for the nuts and bolts should be "0" and not "screwHoleTolerance". This is done correctly for the Z-Carriage (Small gears), but not for the X/Y carriages. (Big gears.)
I believe pull request #55 should be reverted as it is wrong. (https://github.com/CarlosGS/Cyclone-PCB-Factory/commit/58bdfc801b13c2decccf24d2497577d4b9f68449)

The reason is that the nut/bolt sizes that are used, are looked up in the "nuts_and_bolts.scad"-libary. If you follow the references there, you'll notice the sizes are already the maximum allowed according to the sspecifications.
By adding an extra tolerance, you will always end up with STL files that are too large to fit a bolt/nut.
(If using tolerances, they should be negative.)

farhan711, 2016-11-05:
Sorry for interruption but might this information i should share with u all i hope it might help
Let me sum it up:
There are several steps in the toolchain that could theoretically cause a shrinkage of holes:
1. CAD: Exporting to STLs (Low resolution reduces inner diameters if no compensation takes place)
This is known to be an issue, nophead has put quite some time into investigating it. If this is your problem, you can simply fix it by exporting the model with a higher angular resolution.
2. Slic3r: Wrong toolpath
3. Printing: Shrinkage due to the way the plastic is deposited

IMHO If the assumption for the correct toolpath (2) is any good, then printing a high resolution STL file should result in a dimensionally accurate object. To my experience this is NOT the case. Therefore I would challenge the current assumption for the creation of the toolpath. (AFAIK this toolpath simply traces the outlines of the 3d model?)

Solutions:
1. "Change the CAD Model":
It is often suggested to change the model, i.e. the inner diameters of holes, to compensate the shrinkage. This is a workaround, which might be ok for very simple CAD models, for more complex projects it becomes a nightmare. From the professional mechanical engineering viewpoint this is just wrong.
In the CAD stage you define functionality: can a part rotate around another, how much resistance is there to the rotation, etc. You chose nominal sizes and tolerances so they result in the correct fit for the application: Is the bolt in the hole a snug fit, can it be slid in and out, or is it a loose fit with some play. The CAD-Model reflects the functionality though the chosen dimension and the tolerances of paired parts. Manufacturing has then to respect those.

The printed object should have the exact dimensions of the CAD model/STL file. To my and others experience this is currently not the case for vertical holes.
2. "Toolpath Compensation"
For concave toolpaths the extruded plastic seems to be squished more towards the inner radius. The effect becomes obvious in vertical holes where the diameter shrinks. As this is a phenomenon specific to the FDM method, the solution should be implemented in the tool that creates the specific machine code (Slic3r). Maybe the effect could be compensated by moving the toolpath depending on local curvature and extrusion width.

JohanBraeken, 2016-11-05:
Hi Farhan771,

I agree with what you are saying.
I think in this case "Change the CAD model" is a good solution as the issue is not caused by effects in the toolpath or printing process, but by wrong dimensions used to generate the model that should fit an M8 bolt.

The library used to generate the holes and hexagonalshapes for the bolts already uses tolerances and by adding another tolerance in Cyclone on top of that, the generated model is outside of tolerances and too large to fit a bolt snugly.

Let me explain in detail:

The bolts in question are M8 bolts and these are standardised.
The hexagonal shape for such a bolt is suposed to be 15mm from corner to opposite corner and if the generated model is like that, you can say it is according to the specs for M8 bolts.
(See http://www.roymech.co.uk/Useful_Tables/Screws/Hex_Screws.htm)

By default, the Nuts and Bolts library, used by Cyclone, generates the hexagonal shape by creating a cylinder with $fn=6 with the correct diameter for the bolt (+ a neglegible tolerance of 0.001mm added to the readius).

This is how the smaller (perfectly working) gears are generated for the Z-axis in Cyclone.
So far, so good.

However, for larger gears (used in the X and Y-axis) instead of doing it like for the Z-axis, the Cyclone openscad code doesn't use the default "nuts and bolts"-tolerance, but uses a tolerance of (standard) 0.4mm.
Because the "nuts and bolts" code adds this tolerance to the radius, the result is that twice this tolerance (0.8mm) is added to the diameter of the generated cilinder.

By adding this extra tolerance, the generated hexagonal shape to hold the bolt is 15.8mm instead of 15.002mm which is larger than it is suposed to be and therefor bolts will never fit snugly and will always have some play.

I did notice the extra play when trying to fit the bolt. I measured that my printed result was too large, but verified by measuring directly on high resolution STL- files. That is how I discovered the generated design was not according to standard M-bolt sizes and the code contained an error.

So changing the code to omit this second extra tolerance as already done for the Z-axis  is not a workaround, it is fixing a bug.  ;-)

Cuningan, 2016-12-04:
Hello I have the same issue, but not only on big gears, all the m3 nuts holes are much more bigger than the nut and gears axis are bigger than motor axis leading to loosen fit.
Only Z gears are OK.

scottsask, 2017-02-15:
I struggled for a long time with the same issue, just found this thread after finally sorting it out.

I also had to set the tolerance to 0 to have the gears snugly fit over the stepper shafts.

My printer is calibrated, it's definitely this tolerance value.  Hopefully anyone else who is starting a Cyclone CNC project finds this -- the tolerances are in the config.h file.

CarlosGS, 2017-02-25:
I'm so sorry for this issue, when first designing the parts my printers did not have proper calibration and quality was very low. Hence it was necessary to have large tolerances, and the gears did fit OK.

If somebody has the time, please share the corrected STLs. You can create a pull request that updates the problematic STLs and maybe fixing the "double tolerance" issue in the source code for the gears (kindly pointed out by @JohanBraeken). Thank you in advance.

CarlosGS, 2017-02-25:
By the way you can check out as well this nice fork by Engineer2designer:
http://engineer2designer.blogspot.com.es/2017/02/cyclone-pcb-factory-thingiverse.html
It is likely the tolerances have been fixed by our friend! :)

scorpion83, 2017-08-21:
I really like the design of this project and a lot of thought went into it but now that I have finished printing all the parts, I'm extremely disappointed how loose some of the pieces fit due to incorrect tolerances.  I was just bit by this tolerance issue!  @CarlosGS you should update the files here on github with the correct versions so others like myself don't waste a whole weekend printing and a spool of plastic to find out the whole thing needs to be re-printed.  If you don't have the time to update the files with the correct tolerances then I suggest you put in big bold writing that there is an issue with the files so others don't waste their time and money like me and I'm sure many others have

CarlosGS, 2017-08-22:
Sorry for the inconvenience. I've just added a warning in the front readme pointing to this thread.

There are many possible combinations of 3D printers and slicing software, so it is very difficult to provide one single set of STLs that works properly for everybody without requiring some sort of tuning.

Since I do not need to print these parts again, I would appreciate if someone can create a pull request that updates the tolerances in the STLs.

JohanBraeken, 2017-08-23:
Carlos,

I don't completely agree with your view on STLs.

For me, the STL's should always have the correct (desired) value. This
is how it "should" be, the design, the reference.

It is up to the person printing the part to make sure the printer is
calibrated correctly, or to play with slicer settings to off-set
potential shrinkage of material. (This actually depends more on the
filament/material being used, and not on the printer.)

I know it is an easy solution to change the STL. However, as I see it,
you should never fiddle with STL dimensions for issues that are caused
by sub-optimal slicer settings or an un-calibrated printer setup. I
strongly believe issues should be resolved where they are occurring,
and not hidden by compensating for them elsewhere.

Best regards,

Johan.

P.S. I'll try to do a pull request. This could take up to a few days
due to other commitments.

Citeren Carlos Garcia Saura <notifications@github.com>:

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

Links:
------
[1]
https://github.com/CarlosGS/Cyclone-PCB-Factory/issues/57#issuecomment-324164527
[2]
https://github.com/notifications/unsubscribe-auth/AFYrcMNA9kMItjiaTQo01Yxsc9y8tUOAks5sa1AhgaJpZM4ITbXx

CarlosGS, 2017-08-27:
Thanks for your comments Johan.

You are right, for some reason I had a misconception regarding printing tolerances. I think it may be related to having learned CAD/printing at a time where slicing software was in very early stages and difficult to configure.

Now I see that the scad code could have been much more simple by removing the (redundant) code lines that account for tolerances.

Regards,
Carlos

CarlosGS, 2017-09-06:
Thanks to @JohanBraeken and Martin Prochnow (@mprochnow) this issue is now solved.

The other STLs still have many unnecessary tolerances, but the gears must have been the most annoying for sure.
Again, I'm very sorry for the issues caused by my mistaken understanding of tolerances in 3D design.

Closed 2017-09-06.

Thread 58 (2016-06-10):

Nema 17 - Specify load

gsalvati, 2016-06-10:
Can you specify the NEMA 17 stepper motor load / kind on wiki ( Bill of materials )?

CarlosGS, 2016-06-10:
Hi, I have just added it as: "NEMA 17 motor. 1.8 deg, 4.8 kg/cm (or similar)"
Cheers!

gsalvati, 2016-06-10:
Thanks a lot!

gsalvati, 2016-06-10:
On all 3 motors? can I use one with 1.1kg/mm on Z axis?

CarlosGS, 2016-06-10:
Yeah it sounds like it would work. Haven't tried it though.
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

Closed 2016-06-10.

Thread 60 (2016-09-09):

End stops not working with grbl

fisch3r, 2016-09-09:
Hey there,

first all thanks for your great work!

Today I finished my build and everything is working except the end stops. I use Ramps 1.4 + Arduino Mega 2560 in combination with grbl in order to use bCnC. When I start the homing sequence the y-axis crashes into the end stop. The end stop lights up but the motor does not stop.

I connected the x-axis end stop to x-min and the y-axis end stop to y-min. See also the attached image.
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
The switches look like [these](http://g01.a.alicdn.com/kf/HTB1BD8eJpXXXXc5XXXXq6xXFXXXg/1PCS-High-Quality-Mechanical-Endstop-For-Reprap-ramps-1-4-3D-printer-With-independent-packing.jpg).

Is there a command to check the end stop status, like M119? I did not yet try marlin so far.

CarlosGS, 2016-09-12:
Hi, did you try wiping the EEPROM and flashing back GRBL?
I don't recall the command to test endstops :S
The best check would be to measure the voltage level at each RAMPS endstop pin with a multimeter.

lasicmk2, 2016-10-17:
Also, please check while running bCNC, if you push endstop by hand bCNC generate "hard limit" alarm, if not find "command" window in lower right corner of bCNC window ant type "$21=1" - it will activate hard limits. Next try above sequence once more.

CarlosGS, 2017-02-25:
Closing this issue as it refers to firmware and software. If still persists, please submit it again to the most adequate of these:
https://github.com/CarlosGS/grblForCyclone/issues
https://github.com/vlachoudis/bCNC/issues
I hope you did manage to solve it! :-)

Closed 2017-02-25.

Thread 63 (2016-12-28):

grbl 1.1

MoonshineSG, 2016-12-28:
any plans to update to the new version of [grbl](https://github.com/gnea/grbl/) for RAMPS/Cyclone ?

CarlosGS, 2016-12-28:
At the moment I'm quite happy with this version, it has worked very well so
far.

So sorry but I don't plan on updating it any longer.

On 28 Dec 2016 03:31, "ǝuıɥsuooɯ" <notifications@github.com> wrote:

any plans to update to the new version of grbl
<https://github.com/gnea/grbl/> for RAMPS/Cyclone ?

—
You are receiving this because you are subscribed to this thread.
Reply to this email directly, view it on GitHub
<https://github.com/CarlosGS/Cyclone-PCB-Factory/issues/63>, or mute the
thread
<https://github.com/notifications/unsubscribe-auth/ABj3qiolIEd3Fzw8qF6gMAuPtf1tNJF5ks5rMcoQgaJpZM4LWoUZ>
.

MoonshineSG, 2016-12-28:
Yes, it does work quite well. Some unsupported commands, but nothing that can't be worked around.
I was just wondering on the longer term plans. Second sentence answers that.thanks.

Great work, btw.

MoonshineSG, 2016-12-28:
oh... one of the main reasons why 1.1 is interesting is the laser support... just saying...

CarlosGS, 2017-02-25:
Maybe if I build a laser cutter in the future! I'm still waiting for high power laser diodes to drop in price a little bit.

CarlosGS, 2017-02-25:
I've moved this issue to the GRBLforCyclone repo: https://github.com/CarlosGS/grblForCyclone/issues/1

Closed 2017-02-25.

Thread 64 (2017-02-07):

Car wash sponge

ffvdvbhd, 2017-02-07:
Contact Now
Magic sponges, also known as white[ kitchen sponges](http://www.melaminefoam-mfr.com), melamine kitchen scrubs, is open-cell foam with hard inner structure. When used for kitchen sponges, the magic sponge slide over the surface like fine-sandpapers, getting into tiny grooves and pits in the objects being cleaned. On the microscopic level, the microstructure becomes very hard when melamine resin cures into foam.

white kitchen sponges
Rubbing with a slightly moistened foam may remove otherwise "uncleanable" external markings from surfaces. For example, it can remove crayon, magic marker, and grease from painted walls and wood finishing, plastics adhering paints from treated wooden tables, and adhesive residue and grime from hubcaps. If the surface being cleaned is not sufficiently hard, it may be finely scratched by the melamine material. The foam wears away, rather like a pencil eraser, leaving behind a slight residue which can be rinsed off.
Without any detergents, just water stubborn stains can be wipe out easily.It is suitable for wide range, suitable for home, kitchen, bathroom, office, etc. anywhere. Easy to use, can be cut into different sizes according to the shape required.

sponge for kitchen
Cleaning scopes:
1.Ceramic: bowels, dishes, tableware, tea set, sanitary fittings, mosaic tiles, ceramic tiles, etc.
2.Plastic: desk & chair, shower rooms, PVC windows and doors, slippers, ash-bins, toys, etc.
3.Office equipment: computers, printers, duplicators, fax machines, etc.
4.Home appliances: TV, iceboxes, washing machines, air-conditions, micro-wave ovens, electric cookers, etc.
5.Glass: glass doors and windows, ornamental glass, vases, lamps and lanterns, etc.
6.Leather: cars and its interior trim part, leather furniture, leather bags, shoes,etc.
7.Hardware: locksets, sockets, wire, etc.

disposable kitchen sponges

Melamine sponges size and shipping:
The regular sizes of kitchen cleaning sponge is 11.7x6.1x2.5cm (4.6'x2.4'x1'), 10x7x3cm (4'x2.75'x1.2') and etc. As kitchen scrub manufacturer, we provide custom sizes and shapes of melamine sponges. The price varies in accordance to the size and shape. Regular melamine sponge can be hot-pressed or compounded with colorful scouring pads.
We export melamine foam sponges all over the world. The common shipping method is by ship in high-Q container, which ship 68m³of cleaning sponges.

Closed 2017-02-08.

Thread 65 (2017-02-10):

fresas

b4zz4, 2017-02-10:
que tamaño y modelo de fresas usan normalmente para pcb, yo usaba una v1001 pero ahora me esta andando muy malo, nunca andubo demaciado bien la cnc :S

CarlosGS, 2017-02-12:
Hola, [en este link](https://github.com/CarlosGS/Cyclone-PCB-Factory/wiki/List-of-suppliers#consumables) puedes encontrar la lista de herramientas que utilizo, junto a los links de compra en eBay.

Para este tipo de cuestiones te ruego que uses [el foro de Google Groups](https://groups.google.com/group/cyclone-pcb-factory-es).

Un saludo!

Closed 2017-02-12.

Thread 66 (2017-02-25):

Motor doesnt fit.

mcparyk, 2017-02-25:
I have printed a z-spindle cariagge, but my motor collides with hole for threaded rod. I am using NEMA 17 from microcon. Please fix it. This is the last thing before finishing my machine.

CarlosGS, 2017-02-25:
Hi, please check out the assembly guide for the Z axis; the rod is not supposed to go all the way through.

https://github.com/CarlosGS/Cyclone-PCB-Factory/wiki/Assembly-of-the-Z-axis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 (see section 8, image 2)

Let me know if this solves the problem :)

mcparyk, 2017-02-25:
Oh sorry, I placed it wrong... I am so stupid..

CarlosGS, 2017-02-25:
No, I agree that part of the assembly is confusing, many other people had the issue as well. The Z axis would benefit from a re-design.
Oh and don't forget to say hello in [the forum](https://groups.google.com/forum/#!forum/cyclone-pcb-factory) so we can see your build! :-)

Closed 2017-02-25.

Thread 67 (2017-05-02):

Large bearings

mariustupac, 2017-05-02:
Hello! I wanna use some rexroth bearings and they have 16mm outer diameter, can someone point me to right direction on what to modify and where in the openscad files?

kejcbjn, 2017-09-21:
tggg

kejcbjn, 2017-09-21:
Hello! I wanna use some rexroth bearings and they have 16mm outer diameter, can someone point me to right direction on what to modify and where in the openscad files?

kejcbjn, 2017-09-21:
thank you

CarlosGS, 2017-09-21:
Hi, sorry for the delayed response. The bearings are defined here:
https://github.com/CarlosGS/Cyclone-PCB-Factory/blob/master/Source_files/configs/Default_config.h#L99
(List of bearing types: https://github.com/CarlosGS/Cyclone-PCB-Factory/blob/c945f72dcd6b102434cc157c840425447c59051f/Source_files/libs/linear_bearing.scad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 )

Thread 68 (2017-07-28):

bill of materials in spanish

jbrereton6, 2017-07-28:
the bill of materials is in Spanish

falconxperto, 2017-08-08:
maybe u can translate that... xd

jbrereton6, 2017-08-08:
one of the words translates into asparagus

CarlosGS, 2017-08-17:
This made my day :-)
I've translated the page to english language: https://github.com/CarlosGS/Cyclone-PCB-Factory/wiki/Shopping-list

_Espárrago does mean Asparagus ;) In this context, it means grub screw!_

Sorry for the delay and thanks for the feedback. I hope the translation helps!

Closed 2017-08-17.

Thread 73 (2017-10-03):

problem with the archives

OmarCL2002, 2017-10-03:
I can't find the separated archives for printing the pieces, i only find the entire machine, someone help?

CarlosGS, 2017-10-03:
Hi Omar, you can find them here: https://github.com/CarlosGS/Cyclone-PCB-Factory/tree/master/Output_files

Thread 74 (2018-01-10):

BoM redirects to Wiki main page

brnl, 2018-01-10:
Hi,

I'm curious if this project is still alive. I'm trying to research how feasible it is to build the Cyclone 2 but the (**English**) documentation seems outdated.

One problem is the BoM (https://github.com/carlosgs/Cyclone-PCB-Factory/wiki/Bill-of-materials) redirects back to the Wiki main page (https://github.com/carlosgs/Cyclone-PCB-Factory/wiki)

Also, the [suppliers page](https://github.com/carlosgs/Cyclone-PCB-Factory/wiki/List-of-suppliers) contains only dead links.

Is the project still supported or am I better off buying a ready-made kit?

Thanks for your time!

CarlosGS, 2018-01-10:
Hi! I've fixed the link to the BoM in the main wiki page.
However, I think you are right: nowadays it is better (and cheaper) to purchase a generic CNC kit.
Cheers,
Carlos

brnl, 2018-01-10:
Hi @CarlosGS,

Thank you for your honest reply. I love your work, though. Was an awesome initiative!

Cheers,
Bram

CarlosGS, 2018-01-11:
Thanks, and happy milling! :-)

Closed 2018-01-10.

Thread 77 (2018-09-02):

Selling the Cyclone PCB Factory

ShaneOberloier, 2018-09-02:
Hi Carlos -- Sorry for opening a GitHub issue, but it was the only way I could find to contact you - I realize the machine is CCbySA, but I wanted to double check - I am planning to modify this machine and begin selling it on one of my websites. Are you okay with this? Of course I will link back to your work and attribute you and your fellow contributors.

Thanks!
-Shane

Obijuan, 2018-09-03:
Hi Shane!
I am sure that Carlos will answer soon, but in the meantime, I will answer for him: you can shell it for sure! The great thing about the open licences as CCbySA is that you do not have to ask for permission. You can use Cyclone for any purpose (including commercial)

But in any case, It is great to know you like the project and you are planning to improve it and shell it. That's the purpose of the open projects! :-)

Best regars, Juan

CarlosGS, 2018-09-04:
100% agree with Juan, go for it! Looking forward to see your improvements :-)

PS: There is a [Cyclone mail list](https://groups.google.com/forum/#!forum/cyclone-pcb-factory) that is still reasonably active, you can connect with the group there. You'll also find other derivations of the design that may be useful in your design process.

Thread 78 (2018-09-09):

Could I use a dremel multipro 395 with this?

radiomaniac, 2018-09-09:
Hi, sorry this is not an issue but I don't know how to write to Carlos so I'm hoping that maybe if I post here he will read this

I want to make this project but I have a dremel multipro (model 395) could it be possible to use it with this project? Would it be a matter of designing another z carriage or is it just not possible and I have to buy another dremel?

Thanks

electrocbd, 2018-09-09:
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
I have the same dremel model, and I modified the scad source code to
generate the correct z carriage.

Here is the corresponding diff:

index 9c8c49d..218ee9d 100644
--- a/Source_files/configs/Default_config.h
+++ b/Source_files/configs/Default_config.h
@@ -174,10 +174,10 @@
                spindle_holder_bolt_diam = 6;
       
        // --- Spindle Motor ---
-               spindle_motor_diam_top = 51.3;
+               spindle_motor_diam_top = 54.3;
                spindle_motor_diam_top_smaller = 47.5;
                spindle_motor_diam = 47.5;
-               spindle_motor_sidelen = 32;
+               spindle_motor_sidelen = 34;
                spindle_holder_thickness = 8;
                spindle_motor_length = 90;

Anyway, this model is no longer produced, and the resulting z carriage
lacks rigidity (it is also the case with other dremel models)

Good strategy seems to

1 Buy a modern dremel or a spindle
2 Redesign the z carriage

Easier to write than to do ;-)

Regards
electrocbd

radiomaniac, 2018-09-09:
Thanks for the reply. I think I will just sell my dremel and tools as I don't use them and then buy a better dremel or a spindle to make this thing.

CarlosGS, 2018-09-09:
Electrocbd is right on point.
And it is wiser to use a proper DC spindle, the Dremel-type tools are very noisy and get very annoying at some point. My machine still has a Dremel so I wouldn't know which spindle to recommend you.
Please drop by the [Ggroups forum](https://groups.google.com/forum/#!forum/cyclone-pcb-factory), there's much more people and support.
Cheers,
Carlos

radiomaniac, 2018-09-09:
Thanks, I was considering to buy a spindle and I was starting to think where to find the most appropriate one for the cyclone. I will search there, thanks

radiomaniac, 2018-09-10:
By the way, I'm also from Spain, carlos do you know where I can buy the springs? Thanks

CarlosGS, 2018-09-10:
Pasate por el [foro en español](https://groups.google.com/forum/#!forum/cyclone-pcb-factory-es), usa el buscador y si no encuentras lo que necesitas, adelante y manda un correo por allí :-)

radiomaniac, 2018-09-10:
No sabía que hubiera foro en español vaya, que bien. Gracias, buscaré por ahí. Busqué en el inglés pero solo encontré un mensaje preguntando por el tema de los muelles en el que respondías que no sabías de ningun sitio fuera de españa donde conseguirlos. Intentaré buscar en el foro español . Gracias

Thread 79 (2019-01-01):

Regarding Springs

moliata, 2019-01-01:
Hello,
Where can I buy springs with the parameters required for Cyclone PCB Factory. Maybe someone can make them for me? I would gladly pay for that.
Best regards,
Ben.

Helicon007, 2019-01-02:
Hi Ben,

there are no special parameters for the springs. I bought them at a standard Hardware Store/Home depot. They has to fit the threaded rods and should have enough tension to push the sliding bed against the thread, thats all. The springs just reducing the tolerance or movement of the nuts on the thread.

Regards, Helicon

moliata, 2019-01-02:
Hello,
thank you for your response. I am more into hardware and software side, so the physical side of the Cyclone PCB Factory is hard on me. If I correctly understood, these springs should be okay? https://www.aliexpress.com/item/3D-printer-accessories-Ultimaker-2-UM2-spring-fine-print-platform-edging-1-2x15-mm-for-UM2/32818065797.html
Best regards,
Ben
P.S: those springs have 6 turns, that shouldn't be a problem.

Helicon007, 2019-01-02:
Hi Ben,

for 8mm rods they might be to tight. If 9mm is really the outer diameter you end up with 6.6mm inner. If your rods are 6mm they are perfect. In gererall you got the point, those kind of springs are fine for the Cyclone.

Regards, Helicon

moliata, 2019-01-02:
Okay, thanks! So I should get springs which have ~8.5mm inner diameter?
Best regards,
Ben.

Helicon007, 2019-01-02:
Anything bigger than 8, I don‘t know the standard values. The spring has to slide without stucking at the thread. I guess 8.2 - 8.5mm would be fine.

moliata, 2019-01-02:
Awesome, so these should be perfect: https://s.click.aliexpress.com/e/bjOfqQ7q
These follow parameters as well -> 1mm wire diameter, 11mm outer diameter, 15mm length and from what I see in the photo (correct me, if I'm wrong), these have closed end type and 5 turns.
Best regards,
Ben.

Closed 2019-01-03.

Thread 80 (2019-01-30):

Multiple questions

moliata, 2019-01-30:
Hello,
what should be the optimal height for the work base (as well as main)? At the moment, I am able to purchase PlexiGlass sheets with a height between 1-12mm (except 7mm and 9mm).
Best regards,
Ben.

CarlosGS, 2019-01-30:
Hi, I would recommend using wood 15mm thick. It will be easier to machine and also to fix the working materials to the base.

Otherwise the thicker the better since it will be less sensitive to vibrations.

moliata, 2019-01-30:
@CarlosGS thank you! I will be using wood for the main base, but PlexiGlass for the work base. How thick should the work base be.

Helicon007, 2019-01-30:
Hi Ben,

I use a 12mm plexi/acryl plate as base, does the job quiet well.

Regards, Helicon

moliata, 2019-01-30:
Isn't that too thick for the work base (milling area)?

moliata, 2019-01-30:
@CarlosGS regarding vibrations, I will be using 4pcs Rubber Feet from Adafruit, so the base won't be touching the table itself.

CarlosGS, 2019-01-30:
Good idea!

moliata, 2019-01-30:
@CarlosGS in any case, I should still go with a 15mm thick wood base, if I'm using rubber feet? Also, 12mm thick PlexiGlass for the work base (milling area)? I'm in particular looking at having the same thickness main and work as BQ's Cyclone PCB Factory. Lastly, for the "wire management tube", I am looking at a braided sleeves for cables, what size should they be to fit everything in?

CarlosGS, 2019-02-05:
Sorry, I don't remember the exact diameter and don't have the machine at hand to measure it :(

moliata, 2019-02-05:
@CarlosGS when you will have the machine somewhere around, please send the diameter over here, thanks!

CarlosGS, 2019-02-07:
I see my version is not exactly the one from bq, for instance it has a different cable management tube. In my case it is a ~15mm acrylic pipe recycled from some other project.

moliata, 2019-02-07:
Thank you anyways! It seems, it's a 4mm wire management tube.

CarlosGS, 2019-02-09:
Please use the Cyclone Google groups forum for questions, instead of GitHub
issues

El jue., 7 feb. 2019 19:35, Ben <notifications@github.com> escribió:

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

moliata, 2019-02-09:
@CarlosGS sorry! It doesn't seem to be active, so I made issues

Closed 2019-02-05.

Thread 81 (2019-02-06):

Milling Area?

moliata, 2019-02-06:
Hello,
how big is the milling area in Cyclone PCB Factory?
Best regards,
Ben.
P.S: will 10.5x14.8x0.3cm plexiglass sheet fit it?

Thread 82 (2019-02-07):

Mega3D Spacer (Y axis, step 12d)

moliata, 2019-02-07:
Hello,
where can I find the DXF file for acrylic spacer (Y axis, step 12d) used for the Mega3D Board?
Best regards,
Ben.
P.S: @CarlosGS don't you have a file somewhere around? I really need it! Maybe BQ has them, if so, I could send them an email...

CarlosGS, 2019-02-07:
Hi, it should have been here: https://github.com/bq/Cyclone-PCB-Factory/tree/master/bq_additions/Proto/CAD
But they did not upload that particular dxf, probably difficult to get it back from them.

moliata, 2019-02-07:
@CarlosGS do you have the acrylic part yourself (not the file, but the actual part)?

CarlosGS, 2019-02-07:
Nope, in my machine the board is screwed to the base directly. I believe it was designed by @PedroDeOro, maybe he still has the original dxf :-)

moliata, 2019-02-07:
@CarlosGS thanks, I sent an email to Pedro, if he shares it with me, I'll post a PR, thanks!

moliata, 2019-02-12:
@CarlosGS doesn't seem he is going to respond any time soon.

Closed 2020-06-21.

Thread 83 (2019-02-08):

Light metal milling

moliata, 2019-02-08:
Hello,
Is Cyclone PCB Factory okay for milling light metal like aluminum?
Best regards,
Ben.
P.S: I am using Dremel 200 as a spindle tool.

alfadex, 2019-02-08:
I don't think so

CarlosGS, 2019-02-08:
Me neither, I think it is better to use a CNC with a truly rigid structure.

El vie., 8 feb. 2019 18:51, Alfadex <notifications@github.com> escribió:

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

moliata, 2019-02-17:
@CarlosGS it seems you have milled stainless steel (https://groups.google.com/d/msg/cyclone-pcb-factory/K_wEco3CUsA/csFbfF2danwJ) which has more strength than the aluminum. I am not expecting any high-end results with clean edges, I can sand it after the milling. Regarding vibrations, I am using an 8mm thick black acrylic sheet with rubber feet. I would also use 1/8" 2mm ball nose endmill bit.

CarlosGS, 2019-02-19:
Hi Ben, have a look at other versions of Cyclone with a more rigid structure.
I don't have much experience milling metals, but remember it as a pain.

Closed 2019-02-08.

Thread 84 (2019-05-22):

Where can I get that gauge from?

jelkose, 2019-05-22:
Hi,
this is not really an issue, but I have a serious question.

In this excample picture
(https://github.com/CarlosGS/Cyclone-PCB-Factory/blob/master/Media/Cyclone_v2.0_smallBoard2.jpg)
a really cool hole size gauge (and scale) is used.

Can anyone over here tell me what this thing is called and where I can get it?

Regards,

Jelko :-)

CarlosGS, 2019-05-22:
Hi, that awesome part was designed by Pedro de Oro and was custom made for
the company bq.

They used a water jet cutter and a bending machine.

I'm afraid I don't know any supplier for it!

El mié., 22 may. 2019 23:42, jelkose <notifications@github.com> escribió:

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

jelkose, 2019-06-15:
Hmm that's sad.
But the process sounds quite cool!

Thanks for the info!

Closed 2019-06-15.

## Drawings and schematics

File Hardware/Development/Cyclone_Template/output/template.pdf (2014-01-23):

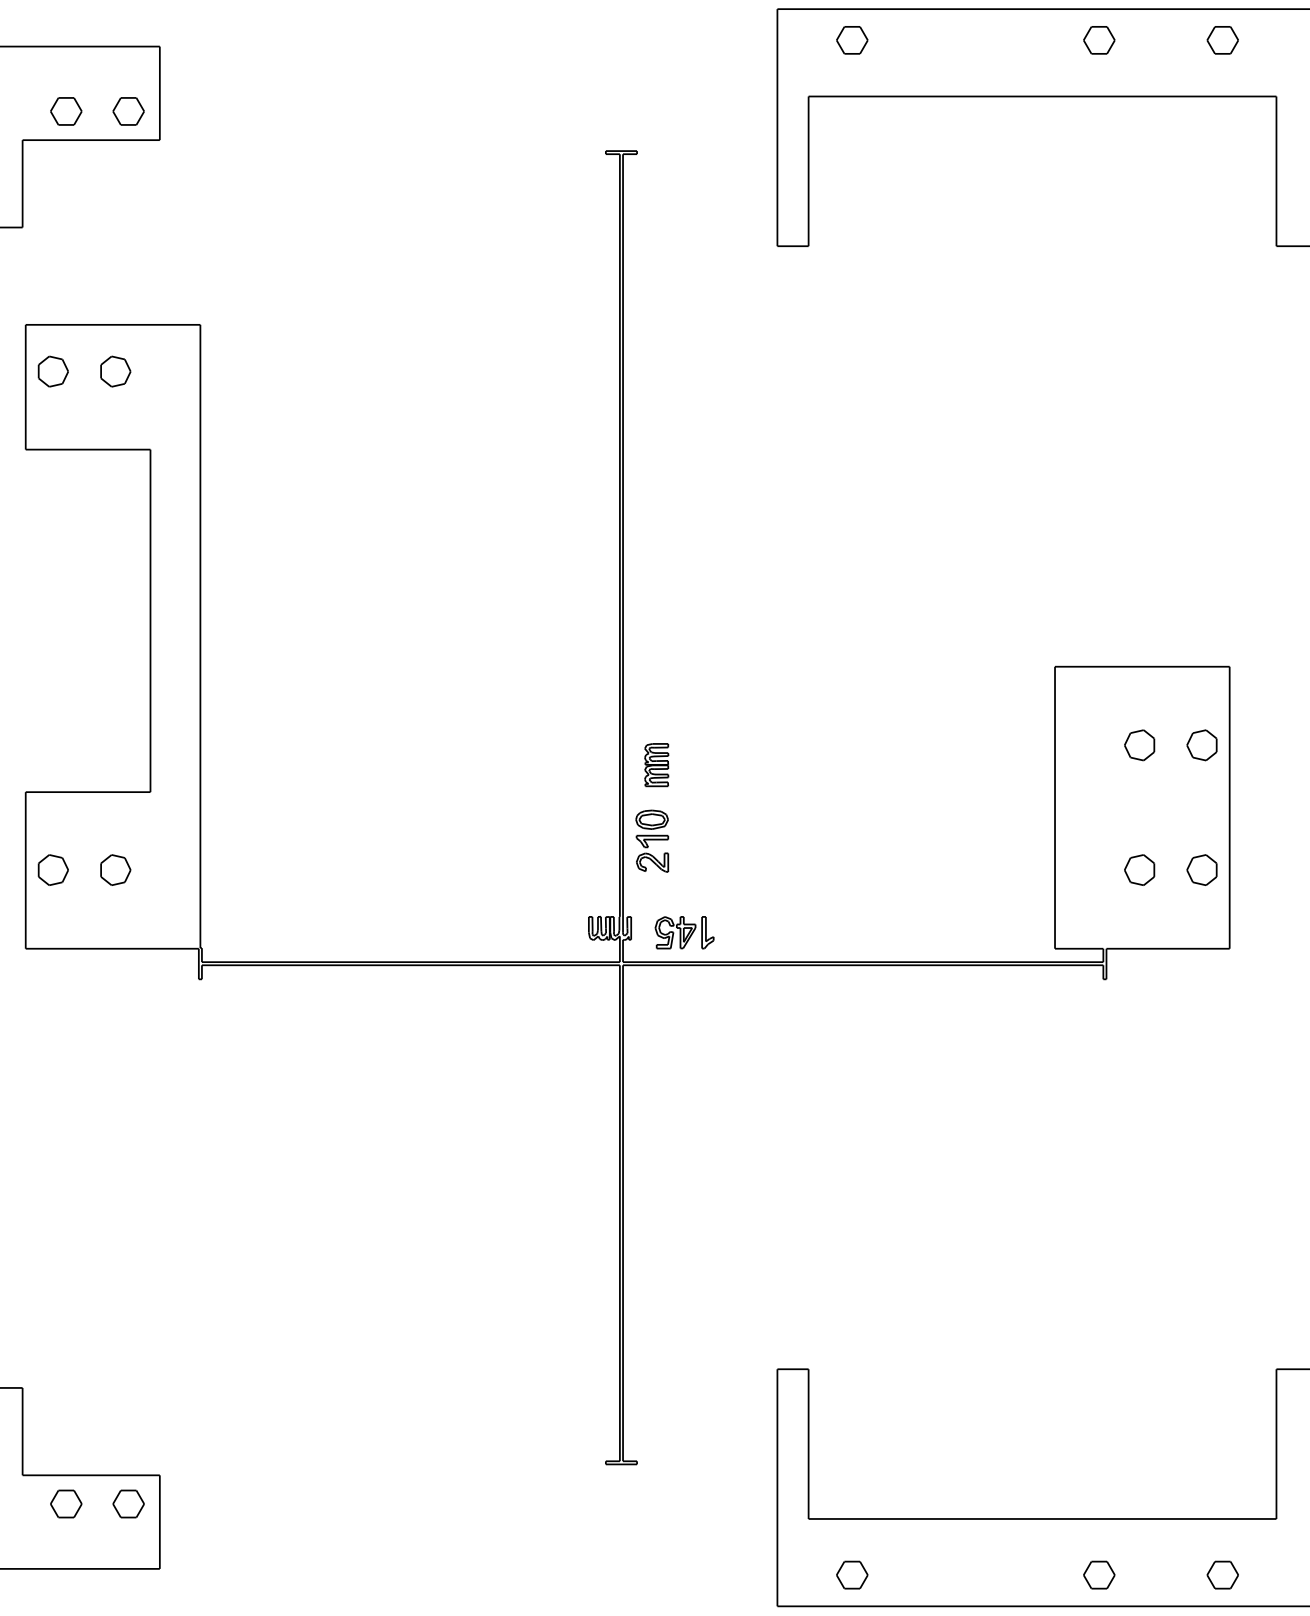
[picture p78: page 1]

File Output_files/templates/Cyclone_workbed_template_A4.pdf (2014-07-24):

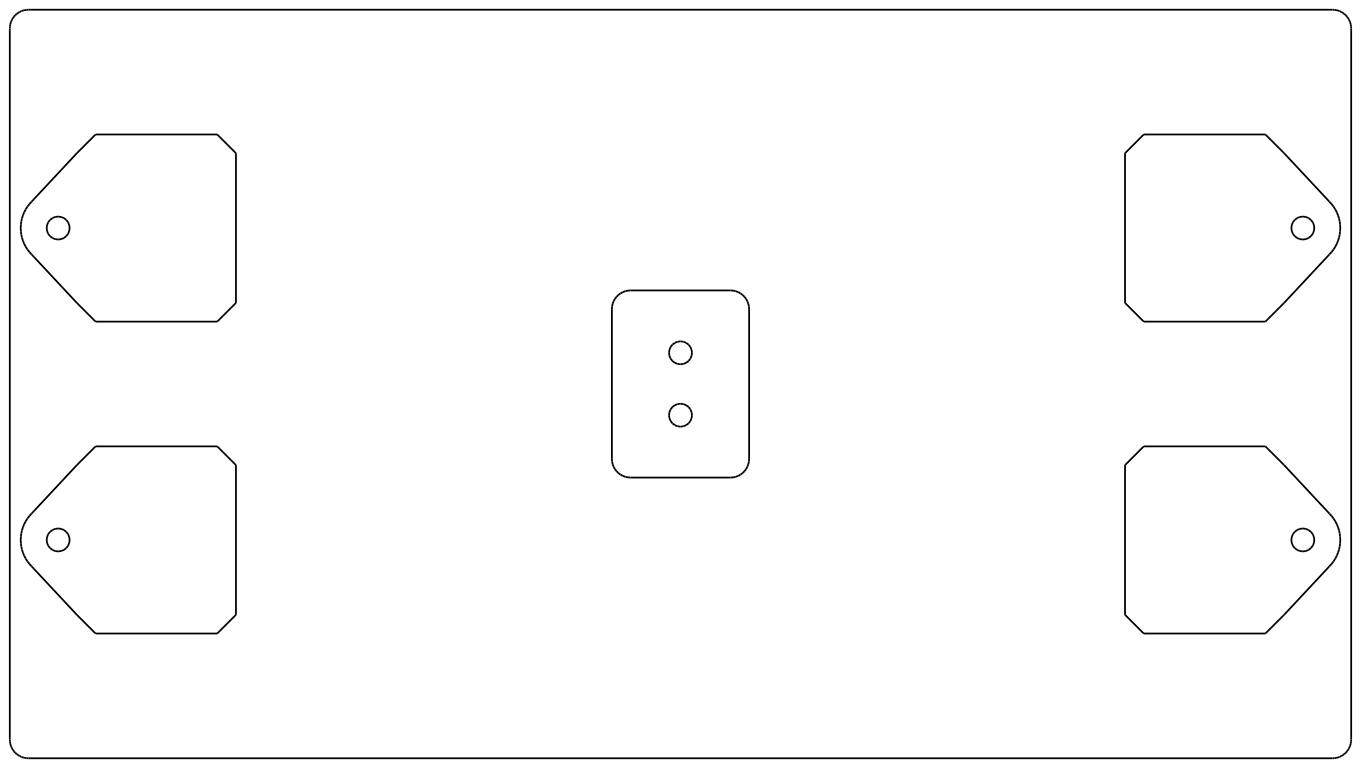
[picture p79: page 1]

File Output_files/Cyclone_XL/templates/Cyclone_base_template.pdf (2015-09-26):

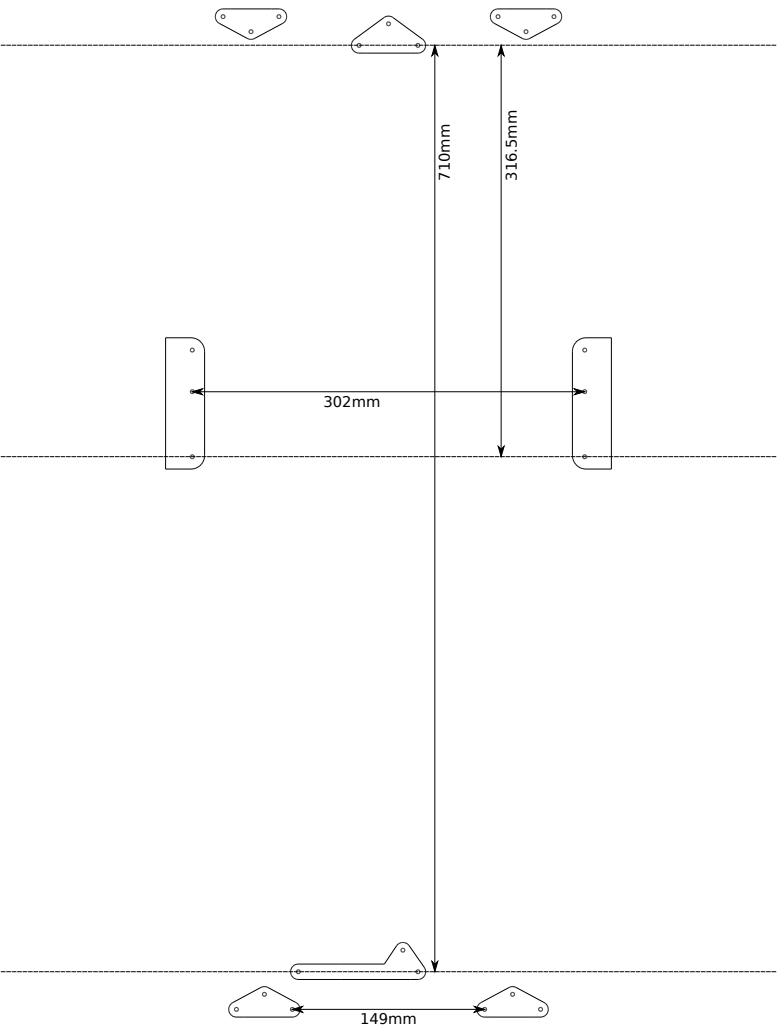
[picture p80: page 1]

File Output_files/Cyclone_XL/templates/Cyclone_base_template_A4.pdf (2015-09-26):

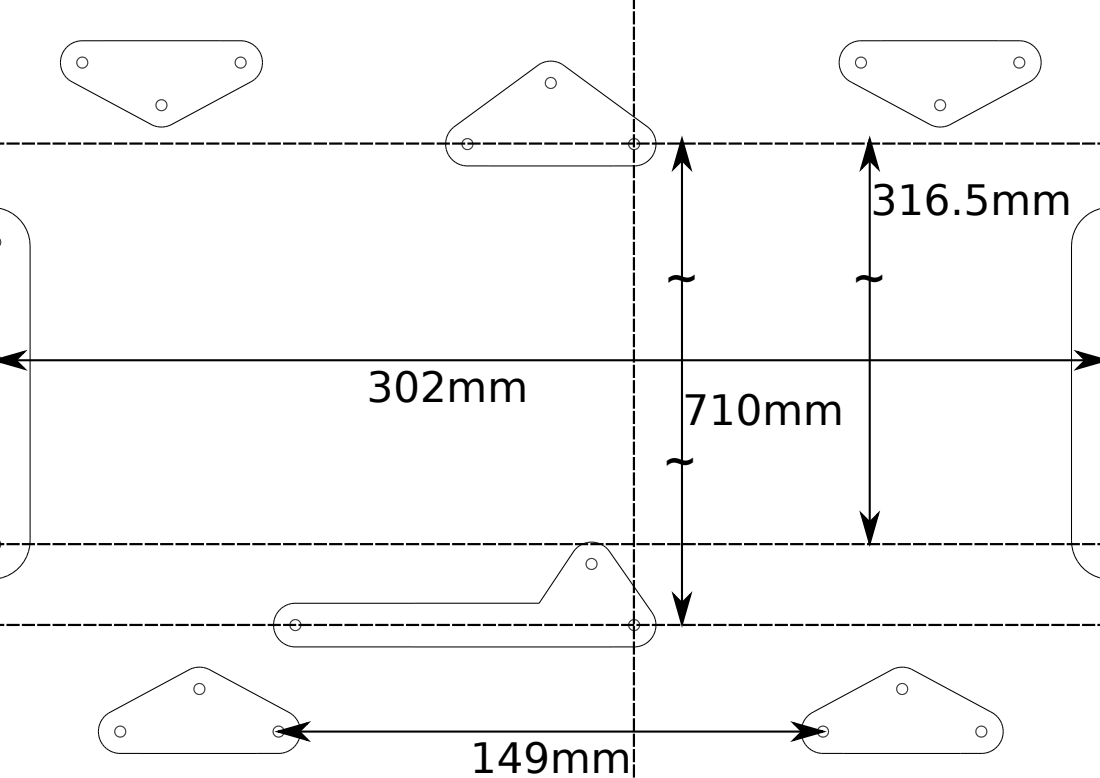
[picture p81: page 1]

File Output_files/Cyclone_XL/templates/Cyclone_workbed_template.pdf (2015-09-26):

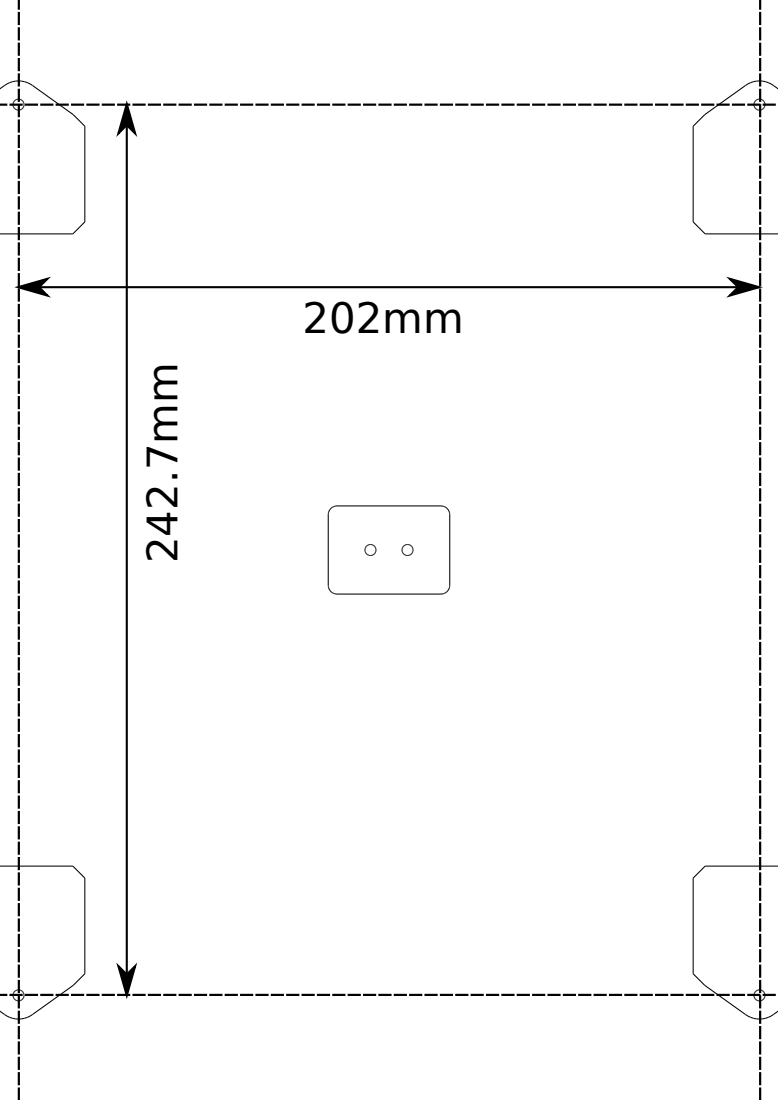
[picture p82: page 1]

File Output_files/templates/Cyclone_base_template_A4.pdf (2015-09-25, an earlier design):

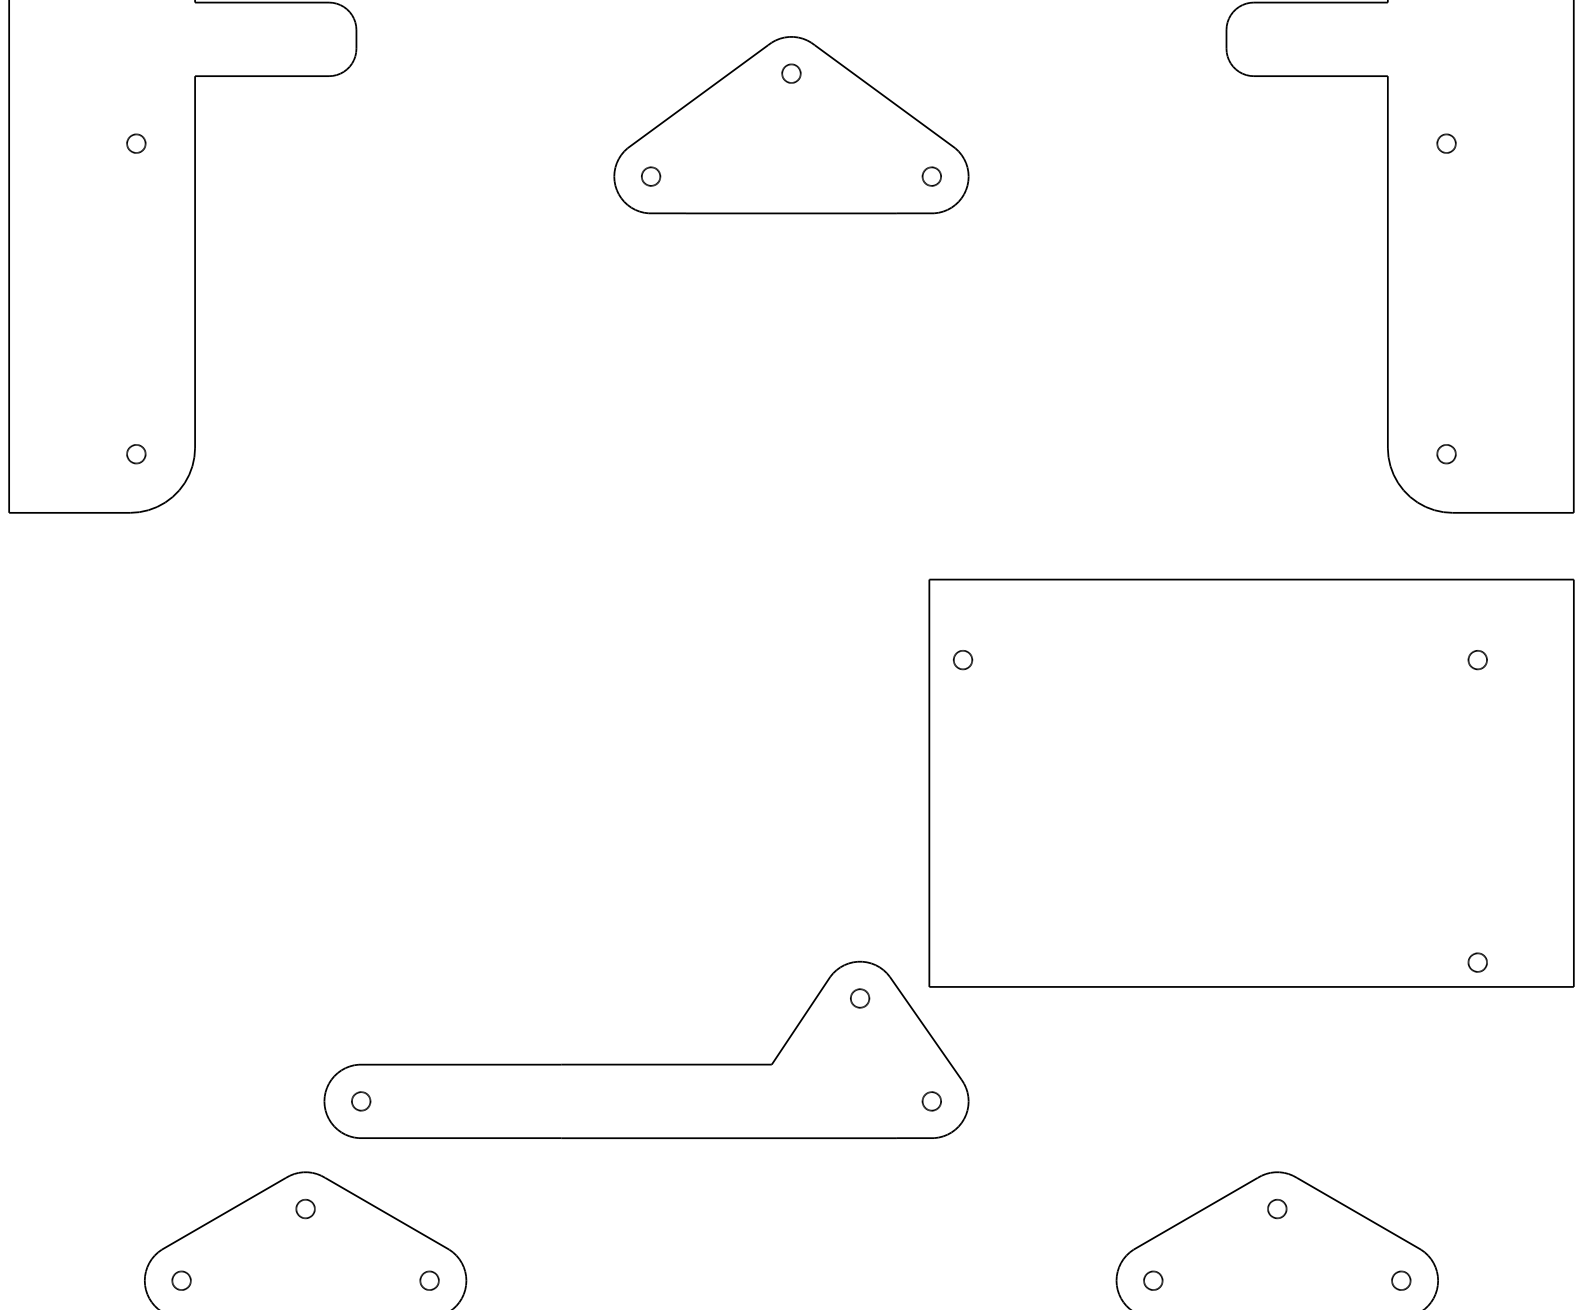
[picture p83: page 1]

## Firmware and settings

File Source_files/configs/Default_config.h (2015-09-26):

// This file is part of Cyclone PCB Factory: an open-source 3D printable CNC machine for PCB manufacture
// http://reprap.org/wiki/Cyclone_PCB_Factory
// Original author: Carlosgs (http://carlosgs.es)
// License: CC BY-SA 4.0 (Attribution-ShareAlike 4.0 International, http://creativecommons.org/licenses/by-sa/4.0/)
// Designed with http://www.openscad.org/

// Default machine config file


// --- Size parameters ---

	// --- Bottom base ---
		base_size_X			= 280 + animatePart(1,overlap=0);
		base_size_Y			= 250 + animatePart(2);
		base_thickness		= 8;
		base_corner_radius	= 20;
		base_corner_res		= 10;
		foot_offset = 25;
		
	// --- Axes reference position ---
	// Note: The reference coordinates are centred like this:
	// Y axis reference is the Y smooth rod end, BACK of RIGHT FRAME
	// X axis reference is the frontal X smooth rod end, RIGHT FRAME
	// Z axis reference is the Z threaded rod, at the height of the Z nut, and relative to the X reference
		axes_Yreference_height	= 40 + animatePart(5);
		axes_Xreference_height	= 74 + animatePart(6); // relative to Y reference
		axes_Zreference_height	= -3 + animatePart(7) + animatePart(9); // relative to X reference

		Cyclone_XL = false;

		axes_Xreference_posY	= -81-animatePart(8)-animatePart(9); // relative to Y reference. Moves the X axis towards the front of the machine
		axes_Zreference_posY	= 14; // relative to X reference. Positions Z rods between the Y rods

		axes_Y_threaded_height = 30 + animatePart(5);

		axes_Ysmooth_separation	= 165 + animatePart(1,overlap=0);
		axes_Xsmooth_separation = 40 + animatePart(9);
		axes_Zsmooth_separation = 40 + animatePart(10,overlap=0);

		
	// --- Work bed ---
		Ycarriage_linearBearingSeparation = 50;
		workbed_size_X			= axes_Ysmooth_separation+50;
		workbed_size_Y			= Ycarriage_linearBearingSeparation+70;
		workbed_thickness		= 8+3;
		workbed_separation_from_Y_smooth_rod = 10;
		PCBholder_height = 10;
		PCB_dimX = 160;
		PCB_dimY = 100;
		PCB_dimZ = 1.6;
		PCB_holder_edge_length = 3;
		
	// --- Z carriage ---
	  Z_carriage_wall_thickness = 9;
	  Z_carriage_wall_width = 54;		
		
  // --- X frames ---
	  X_frames_additional_thickness = 5;
		X_frame_footThickness = 10;
		X_frame_corner_radius = 10;
		X_frame_FrontalThickness = 15;
		X_backlash_armThickness = 30;
		X_motorWallSeparation = 5;
		X_motorRotatedOffset = 5;
		X_gearWallSeparation = 5;
		
  // --- Y frames ---
		Y_frame_footThickness = 10;
		Y_motorWallSeparation = 5;
		Y_motorRotatedOffset = 5;
		Y_gearWallSeparation = 5;
		Y_foot_additional_separation = 5;
		Y_endstopHolderRotation = 5;
		Logo = true; // Add logo to the Y Smooth Rod Idlers
		
	// --- Axes sizes ---
	// *_rodLen = length
	// *_rodD = diameter
		// Y smooth rod
			axes_Ysmooth_rodLen	= 210 + animatePart(2);
			axes_Ysmooth_rodD	= 8.5 + animatePart(4,dist=5);
		// Y threaded rod
			axes_Ythreaded_rodLen	= axes_Ysmooth_rodLen-10;
			axes_Ythreaded_rodD	= 8.5 + animatePart(4,dist=5);
		// X smooth rod
			axes_Xsmooth_rodLen	= 250 + animatePart(1,overlap=0);
			axes_Xsmooth_rodD	= 8.5 + animatePart(4,dist=5);
		// X threaded rod
			axes_Xthreaded_rodLen	= axes_Xsmooth_rodLen+50;
			axes_Xthreaded_rodD	= 8.5 + animatePart(4,dist=5);
		// Z smooth rod
			axes_Zsmooth_rodLen	= 110 + animatePart(3);
			axes_Zsmooth_rodD	= 8.2 + animatePart(4,dist=5);
		// Z threaded rod
			axes_Zthreaded_rodLen	= 90;
			axes_Zthreaded_rodD	= 8.5 + animatePart(4,dist=5);
			
	// --- Bearings ---
		Y_linearBearingModel = "LM8UU";
		X_linearBearingModel = "LM8UU";
		X_linearBearingSeparation = 0;
		Z_linearBearingModel = "LM8UU";
		Z_threaded_rodBearingModel = 608;
		Y_threaded_rodBearingModel = 608;
		Y_threaded_rodBearingDepth = 3;
		X_threaded_rodBearingModel = 608;
		X_threaded_rod_bearingDepth = 3;
		
	// --- Steppers ---
		//Y_motorModel = Nema17;
		//X_motorModel = Nema17;
		//Z_motorModel = Nema17;
		Z_motor_adjust_margin = 5;

	// --- Screw sizes --- 
	// M3, M4, etc (integers only), at the moment only M3 and M4 will work.
		Y_frontFrame_footScrewSize = 3;
		Y_backFrame_footScrewSize = 3;
		Y_rightSmoothRodIdler_footScrewSize = 3;
		X_Frame_footScrewSize = 3;

		Y_threaded_rodNutSize = 8;
		X_threaded_rodNutSize = 8;
		Z_threaded_rodNutSize = 8;
		
		Y_nutHolder_screwSize = 3;
		Y_singleLinearBearingHolder_screwSize = 3;
		Y_PCBholder_screwSize = 3;
		
		Y_backlash_washer_D = 15.8;
	  Y_backlash_washer_thickness = 1.6;
		X_backlash_washer_D = 15.8-0.5;
		X_backlash_washer_thickness = 1.6-0.9;

		X_carriage_screwSize = 3;
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

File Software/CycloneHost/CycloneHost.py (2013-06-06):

#!/usr/bin/python

###### Cyclone Host v1.0 ######
#
# DESCRIPTION:
#   Controller for the Cyclone PCB Factory:
#     "a 3D printable CNC machine for PCB manufacture" (http://www.thingiverse.com/thing:49484)
#   This software has been tested with a Sanguinololu board running a modified Marlin firmware
#   that supports the G30 probing G-code.
#
# AUTHOR:
#   Carlosgs (http://carlosgs.es)
# LICENSE:
#   Attribution - Share Alike - Creative Commons (http://creativecommons.org/licenses/by-sa/3.0/)
#
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
# CREDIT:
#   This script was created using as a base:
#     "Upload GCode to SpereBot" by Tgfuellner http://www.thingiverse.com/thing:9941 (CC-BY-SA)
#   Please refer to http://carlosgs.es for more information on this probing method
#
# REQUISITE:
#   http://pyserial.sourceforge.net
#   Installation on Ubuntu: sudo aptitude install python-serial
#
######################################

# Begin modules
import sys
import serial
import time
from datetime import datetime

from helper import *
# End modules

# Begin configuration. It is overwritten when running setup(baudrate, device)
BAUDRATE = 115200
DEVICE = "/dev/ttyUSB0"
Emulate = 0
# End configuration

lastDrillPos = [0,0,0]

seconds_wait = 0.5 # Delay used when re-trying to send/receive from the serial port [seconds]
serial_timeout = 5 # Timeout for the serial port [seconds]

OK_response = "ok" # First two characters of an OK response (case insensitive)

CNC_Machine = []

def connect(baudrate, device, emulate = 0):
	global CNC_Machine, Emulate
	BAUDRATE = baudrate
	DEVICE = device
	print "Connecting to Cyclone..."
	if emulate == 0:
		CNC_Machine = serial.Serial(DEVICE, BAUDRATE, timeout = serial_timeout)
		Emulate = 0
	else:
		Emulate = 1
		print "EMULATING MACHINE!"
	print "Serial port opened, checking connection..."
	time.sleep(2)
	checkConnection()
	print "Connected!"

def flushRecvBuffer(): # We could also use flushInput(), but showing the data that is being discarded is useful for debugging
	if Emulate:
		return
	while CNC_Machine.inWaiting() > 0:
		response = CNC_Machine.readline()
#		if response != '': print "IGNO: ", response
		time.sleep(seconds_wait) # Wait some milliseconds between attempts

def sendLine(line):
	flushRecvBuffer()
	if Emulate == 0:
		CNC_Machine.write(line)
#	print "SENT: ", line

def recvLine():
	if Emulate:
		response = "ok Z30\n" # Asume OK + Z probing result
	else:
		response = CNC_Machine.readline()
#	if response != '': print "RECV: ", response
#	else: print "RECV: Receive timed out!"
	return response

def recvOK():
	response = recvLine()
	if response[:2].lower() == OK_response.lower():
		return 1
	return 0

def waitForOK(command="",timeoutResend=30): # This is a blocking function
#	print "Waiting for confirmation"
	i = 0
	cmnd = command[:3].lower()
	timeoutResend = float(timeoutResend)
	#timeoutResend = 5.0 # Resend command every 5 seconds, error recovery
	#if cmnd == "g28": timeoutResend = 60.0 # Homing moves will take more than 5 seconds
	i_timeout = int(timeoutResend/float(serial_timeout+seconds_wait))
#	print "i_timeout",i_timeout
	while recvOK() != 1:
		print "  Checking again... timeout:",i_timeout
		time.sleep(seconds_wait) # Wait some milliseconds between attempts
		if cmnd != "g30" and i >= i_timeout: # WARNING: Commands that take >5s may have problems here!
			print "  WATCHOUT! RESENDING:",command
			sendLine(command)
			i = 0
		else:
			i = i + 1

def sendCommand(command,timeoutResend=15): # Send command and wait for OK
	sendLine(command)
	waitForOK(command,timeoutResend)

def checkConnection():
#	print "Checking the connection..."
	sendLine("G21\n") # We check the connection setting millimiters as the unit and waiting for the OK response
	time.sleep(0.5)
	while recvOK() != 1:
		sendLine("G21\n")
		time.sleep(seconds_wait) # Wait some milliseconds between attempts

def homeZXY():
	global lastDrillPos
	print "Homing all axis..."
	timeoutResend=30
	sendCommand("G28 Z0\n",timeoutResend) # move Z to min endstop
	sendCommand("G28 X0\n",timeoutResend) # move X to min endstop
	sendCommand("G28 Y0\n",timeoutResend) # move Y to min endstop
	if Emulate:
		time.sleep(2)
	lastDrillPos = [0,0,0]
	print "Done homing"

def moveXYZ(X, Y, Z, F):
	global lastDrillPos
#	print "Moving to:"
	if F <= 0:
		print "ERROR: F <= 0"
	sendCommand("G1 X"+floats(X)+" Y"+floats(Y)+" Z"+floats(Z)+" F"+floats(F)+"\n")
	if Emulate:
		dist = ((X-lastDrillPos[0])**2+(Y-lastDrillPos[1])**2+(Z-lastDrillPos[2])**2)**0.5 # [mm]
		speed = float(F)/60.0 # [mm/s]
		time.sleep(float(dist)/speed)
	lastDrillPos = [X,Y,Z]

def moveXY(X, Y, F):
	global lastDrillPos
#	print "Moving to:"
	if F <= 0:
		print "ERROR: F <= 0"
	sendCommand("G1 X"+floats(X)+" Y"+floats(Y)+" F"+floats(F)+"\n")
	if Emulate:
		dist = ((X-lastDrillPos[0])**2+(Y-lastDrillPos[1])**2)**0.5 # [mm]
		speed = float(F)/60.0 # [mm/s]
		time.sleep(float(dist)/speed)
	lastDrillPos = [X,Y,lastDrillPos[2]]

def moveZ(Z, F):
	global lastDrillPos
#	print "Moving Z absolute:"
	if F <= 0:
		print "ERROR: F <= 0"
	sendCommand("G1 Z"+floats(Z)+" F"+floats(F)+"\n")
	if Emulate:
		dist = abs(Z-lastDrillPos[2]) # [mm]
		speed = float(F)/60.0 # [mm/s]
		time.sleep(float(dist)/speed)
	lastDrillPos = [lastDrillPos[0],lastDrillPos[1],Z]

def moveZrel(Z, F):
	global lastDrillPos
#	print "Moving Z relative:"
	if F <= 0:
		print "ERROR: F <= 0"
	sendCommand("G91\n") # Set relative positioning
	sendCommand("G1 Z"+floats(Z)+" F"+floats(F)+"\n")
	if Emulate:
		dist = abs(Z) # [mm]
		speed = float(F)/60.0 # [mm/s]
		time.sleep(float(dist)/speed)
	lastDrillPos = [lastDrillPos[0],lastDrillPos[1],lastDrillPos[2]+Z] # Relative movement
	sendCommand("G90\n") # Set absolute positioning

def moveZrelSafe(Z, F):
	if F <= 0:
		print "ERROR: F <= 0"
	print "Moving Z", Z, "mm safely..."
	sendCommand("M121\n") # Enable endstops (for protection! usually it should **NOT** hit neither the endstop nor the PCB)
	moveZrel(Z, F)
	dist = abs(Z) # [mm]
	speed = float(F)/60.0 # [mm/s]
	wait = float(dist)/speed # [s]
	time.sleep(wait) # Wait for the movement to finish, this way the M121 command is effective
	print "   Done moving Z!"
	sendCommand("M120\n") # Disable endstops (we only use them for homing)

def probeZ():
	print "Probing Z"
	sendLine("G30\n") # Launch probe command
	response = recvLine() # Read the response, it is a variable run time so we may need to make multiple attempts
	while response == '':
		#print "."
		time.sleep(seconds_wait) # Wait some milliseconds between attempts
		response = recvLine()
	response_vals = response.split() # Split the response (i.e. "ok Z:1.23")
	if response_vals[0][:2].lower() == OK_response.lower():
		Zres = response_vals[1][2:] # Ignore the "Z:" and read the coordinate value
		print "Result is Z=",Zres
		return float(Zres)
	return 400 # Error case, don't worry: it has never happened :)
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

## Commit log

2013-05-25 First commit, added all the existing parts for v0.9.5
    [Cyclone.stl, X_carriage.scad, X_carriage.stl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]
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2013-05-25 Improved the serial port management, fixed some bugs. Code commenting and cleanup.
    [Zprobe.py]
2013-05-25 This scripts shows the error between measures made in different days with the same PCB
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2013-05-25 Create motor_stand_2_screw_terminals.stl
    "y" motor stand provided with 2 bases/screw terminals. Seems to be much more robust than the single legged version.
    If needed I can upload de .scad file although it is not following the programming style of the original file, it is more an add-on.
    [motor_stand_2_screw_terminals.stl]
2013-05-26 Improved Y axis with Yopero's suggestion. Z carriage shows the name of the machine, using orbitron.dxf font from Write.scad. Updated templates and renders. Updated README to show changes.
    [Cyclone.stl, Z_carriage.scad, Z_carriage.stl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]
2013-05-26 Removed Yopero's STL for the Y axis to avoid confusion. Added video to the README
    [motor_stand_2_screw_terminals.stl]
2013-05-26 Improved frames: thicker stands + easier motor adjustment
    [frame.scad, frame.stl]
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2013-05-28 Added Yopero's improvement for the Y axis (idle stand)
    [Cyclone.stl, idle_stand.scad, idle_stand.stl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]
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2013-05-28 More work regarding: gcode parsing, optimization and visualization CycloneHost is a python module now
    [printshield-1.0-B_Cu.gtl, printshield-1.0-Edge_Cuts.gbr, printshield-1.0.drl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]
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2013-05-29 Added 2&3 extra tool passes (for more clearance). Fixed bug when parsing oval shapes from gerber files.
2013-05-29 Implemented the gcode viewer as a module. Bugfix & code cleanup
    [GcodeParser.py, GcodeViewer.py]
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2013-05-30 More tests, improvements/fixes on the viewer, parser, sender, gerber2gcode... etc
    [CycloneHost.py, GcodeParser.py, GcodeViewer.py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]
2013-06-01 Improvements in the GUI, Gcode Parser, Gcode Viewer and Bugfix in Cyclone Host. Now emulator works 100%
    [CycloneHost.py, GcodeParser.py, GcodeViewer.py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]
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2013-06-01 Thicker version of the Y axis motor/idle stands
    [idle_stand.stl, motor_stand.scad, motor_stand.stl]
2013-06-01 Updated templates to match new Y motor axis. Added the new gears (1.4 ratio, being tested)
    [Cyclone.stl, motor_gear.scad, motor_gear.stl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]
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2013-06-02 Larger hole for the Z threaded rod in the bottom piece
    [Z_carriage.scad, Z_carriage_bottom.stl, Z_carriage_old.scad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]
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2013-06-06 More software tests, bugfix... etc
    [DTMF_Shield-B_Cu.gbl, DTMF_Shield-Edge_Cuts.gbr, DTMF_Shield.drl]
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2013-07-29 Fixed mirroring, thanks Tom for noticing!
    [frame.scad, frame_nomotor.stl]
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2013-08-03 Added flat DXFs for milling/cutting the frames instead of printing (as proposed by Xander in the mail list)
    [frame.dxf, frame_flatDXFs.scad, frame_nomotor.dxf]
2013-08-05 Vertical Z smooth rod holes made smaller so they fit tight
    [X_carriage.scad, X_carriage.stl]
2013-09-08 add X carriage nut holder for 6.2mm thick nuts
    [X_carriage_nut_holder_6.2mm.stl]
2013-09-13 Increased thickness of the smooth rod fix. Thanks Harry Binnema for reporting the issue!
    [smooth_rod_fix.scad, smooth_rod_fix.stl, smooth_rod_fix_x4.stl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]
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2013-09-26 Re-structuration of the repository, updated readme files for each section
    [Cyclone.stl, X_carriage.scad, X_carriage.stl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]
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2013-09-26 Added improvements by Harry Binnema: better gears and symmetric Z carriage
    [Cyclone.stl, Z_carriage.scad, Z_carriage_bottom.stl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]
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2013-10-10 code refactoring for better adjusting wood base dimension
    [template.scad]
2013-10-10 code refactoring for better adjusting final X smooth/threaded rod length
    [template.scad]
2013-10-10 code refactoring for better adjusting final Y smooth/threaded rod length
    [template.scad]
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2013-10-16 1. move M3 x 8mm grub screw to motor_gear.scad 2. more comments 3. BlackPaint micro switch
    [motor_gear.scad, motor_stand.scad]
2013-10-16 add M3 x 8mm grub screw to attach Gear to motor shaft
    [motor_gear.scad]
2013-10-16 Y micro switch assembly was wrong
    [motor_stand.scad]
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2013-10-16 fix motor gear
    [frame.scad]
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2013-10-16 two of 2.9 x 13 mm self tapping scres for each smooth rod fix
    [smooth_rod_fix.scad]
2013-10-16 2.9 x 13 mm was a little too short, use 2.9 x 16 mm instead
    [smooth_rod_fix.scad]
2013-10-16 add Y smooth rod fix
    [frame.scad]
2013-10-16 a minor fix
    [smooth_rod_fix.scad]
2013-10-16 add Y smooth rod fix add self tapping screw 2.9 x 16 mm
    [Y_rod_idler.scad, template.scad]
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2013-10-19 add self tapping screw for attaching linear bearing holder to work bed
    [linear_bearing_holder.scad]
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2013-10-20 fine tune smooth rod and threaded rod length of X and Y axes
    [template.scad]
2013-10-20 Fixed crlf issue of *.scad files
    [motor_gear.scad]
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2013-10-20 fix placement of nuts
    [Z_carriage.scad]
2013-10-21 fix "Non-Plastic Parts" for machine base, work bed, smooth rod, and thread rod.
    [template.scad]
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2013-10-21 1. refactor module rod 2. move Z threaded rod from X_carriage.scad to Z_carriage.scad because it is stick to Z_carriage.
    [X_carriage.scad, Z_carriage.scad, template.scad]
2013-10-22 fix compile WARNING: Ignoring unknown variable 'length'.
    [Z_carriage.scad]
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2013-10-23 Re-formating "Non-Plastic Parts" messages from console. It's easier to be processed in Excel to figure out quantity of each part.
    [X_carriage.scad, Y_nut_holder.scad, Y_rod_idler.scad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]
2013-10-23 fix redundant message
    [frame.scad]
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2013-10-27 fix X End_Stop_Holder and re-position both PCB_vise_1s to accomandate X travel reduced by X End_Stop_Holder
    [frame.scad, template.scad]
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2014-01-18 A fake Spindle that holds a pen to draw pcb board instead of milling
    working video: http://youtu.be/mdT-6VdgRn0
    [SpindlePen.scad]
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2014-04-04 Disabled ENDSTOPS_ONLY_FOR_HOMING since it was causing issues with probing
    [Configuration_adv.h]
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2014-07-23 Added workbed DXF generation. Updated anti-backlash part measures
    [Cyclone.scad, Cyclone_Y_carriage.scad, Cyclone_Ycarriage_nutHolder.stl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]
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2014-08-03 Updated README, re-structured the folder for output files, separated inherited files into another folder
    [Cyclone_base_8mm.dxf, Cyclone_base_drills.dxf, Cyclone_base_outline.dxf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]
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2014-08-05 Improved X carriage, increased frame height, fixed Z carriage
    [Cyclone.scad, Cyclone_X_carriage.scad, Cyclone_Xcarriage.stl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]
2014-08-05 Added note regarding OpenScad default parameters, added PCB holder (work in progress)
    [Cyclone.scad, Cyclone_X_carriage.scad, Cyclone_Y_carriage.scad]
2014-08-06 Fixed X carriage
    [Cyclone.scad, Cyclone_X_carriage.scad, Cyclone_Xcarriage.stl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]
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2014-08-08 Added templates, fixed PCB holder tolerances, added Z gears
    [Cyclone_Y_carriage.scad, Cyclone_Ycarriage_PCBholders.stl, Cyclone_fullPlate_8aug2014.stl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]
2014-08-12 Added shorter version of the frames
    [Cyclone_XleftFrame.stl, Cyclone_XrightFrame.stl]
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2014-08-27 Added endstop holder for the Y axis, inverted base screws
    [Cyclone.scad, Cyclone_X_frames.scad, Cyclone_XleftFrame.stl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]
2014-08-28 Updated Y carriage parts (better endstop integration, softer linear bearing holders). Integrated X endstop in X right frame
    [Cyclone_X_frames.scad, Cyclone_XrightFrame.stl, Cyclone_Y_carriage.scad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]
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2014-08-29 Thickened text, updated tolerances
    [Z_carriage_mod.scad, Z_carriage_mod.stl]
2014-09-01 Updated shorter frames, updated Readme and template names
    [Cyclone_XleftFrame.stl, Cyclone_XrightFrame.stl]
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2014-09-02 Increased M8 rod tolerance, renamed files for easier identification
    [Cyclone_Y_frames.scad, Cyclone_YbackFrame.stl, XYmotor_gear.scad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]
2014-09-02 Tuned tolerances, renamed files
    [Cyclone_Zcarriage.scad, Cyclone_Zcarriage.stl]
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2014-09-08 Updated X carriage with anti-backlash spring system
    [Cyclone_X_carriage.scad, Cyclone_Xcarriage.stl]
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2014-09-11 Updated frames: Rotated motor 5deg, added wire slots, added crocodile clip holders
    [Cyclone_X_frames.scad, Cyclone_XleftFrame.stl, Cyclone_XrightFrame.stl]
2014-09-12 Updated shorter frames to the latest version
    [Cyclone_X_frames.scad, Cyclone_XleftFrame.stl, Cyclone_XrightFrame.stl]
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2014-09-14 Customized color visualization in OpenScad. Added L top supports for PCB holder
    [Cyclone.scad, Cyclone_X_carriage.scad, Cyclone_X_frames.scad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]
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2014-09-17 Renamed STLs, shorter names
    [Cycl_XYgearCover_x2.stl, Cycl_XYmotor_gear.stl, Cycl_XYrod_gear.stl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]
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2014-11-04 + Electronic Case + New .dxf of Base, Workbed and Calibration electrode
    [Configuration.h, Configuration_adv.h, Cycl_Electronic_case.fcstd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]
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2014-11-05 Fixed paths in scad scripts
    [Cycl_X_frames.scad, Cycl_Y_carriage.scad, Cycl_Y_frames.scad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]
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2014-11-29 Added proper screw cap values
    Fixed the TODO: proper screw cap values
    Based on: http://www.roymech.co.uk/Useful_Tables/Screws/cap_screws.htm
    Diameter is pulled from the table METRIC_BOLT_CAP_DIAMETERS and the cap height is the metric size of the bold.
2014-11-29 Update standard_parts.scad
    Fixed: "TODO (from MCAD): proper screw cap values: instead of "height" will use METRIC_BOLT_CAP_HEIGHTS[size]+tolerance" this is not necessary because the cap height is the bold size so M3 cap is 3mm heigh.
    Also fixed some tolerances because they where terrible big. On my print a M3 hole could fit a M4 bold and in the nut holder the nut could almost turn around.
    Removed radius from hole_for_screw and hole_for_nut to clean up the code and it fixed errors in the STL output of OpenSCAD.
2014-11-29 Fixed bolt size issue
    Bolt size of the pcb holder could not be chanced. Now it can
    [Cycl_Y_carriage.scad]
2014-11-29 StepperMotor mount fix
    StepperMotor mount dint render
2014-11-30 Screw Size customization
    Moved the screw size settings to the Cyclone.scad file for better screw size customization
    [Cyclone.scad]
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2014-11-30 Add support for rendering gears
    Replaced the gear mock-ups with real gears and added the nuts on the X-rod
    [Cycl_X_frames.scad]
2014-11-30 Add support for rendering gears
    Replaced the gear mock-ups with real gears
    [Cycl_Y_frames.scad]
2014-12-01 Fix for wrong left/right frame render
    fix for issue https://github.com/carlosgs/Cyclone-PCB-Factory/issues/27
    [Cyclone.scad]
2014-12-06 Merged Cycl_Z_carriage.scad and Inherited_files/Cycl_Z_carriage.scad
    Merged Cycl_Z_carriage.scad and Inherited_files/Cycl_Z_carriage.scad to a working file for the Cyclone.scad rendering
    [Cycl_Z_carriage.scad]
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2014-12-07 Gears fix and improvement
2014-12-07 Added configs/Default_config.h
    Added configs/Default_config.h to make it easy to chance parameters like
    screw size and tolerances
    [Cycl_X_carriage.scad, Cycl_X_frames.scad, Cycl_Y_carriage.scad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]
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2014-12-09 Added 2 more screw and nuts
    added screw and nuts to the y nut holder and fixed a hight error for the
    pcb holder screws
    [Cycl_Y_carriage.scad]
2014-12-09 Position render fix and little code cleanup
    [Cycl_X_carriage.scad, Cycl_X_frames.scad, Cycl_Y_carriage.scad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]
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2014-12-09 Revert "Added support for an alternitive z-carriage"
    This reverts commit 0e71ad30f3fd308029976cd0b269681b77342386.
    [Cycl_X_carriage_alt.scad, Cycl_Z_carriage_alt.scad, Cyclone.scad]
2014-12-29 Parameterized tolerances for the gears
    [Cycl_X_frames.scad, Cycl_Y_frames.scad, Cyclone.scad]
2015-01-21 Increased nut tolerance
    [XYmotor_gear.scad]
2015-02-04 Fixed tolerances
    [Cycl_Z_carriage.scad]
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2015-02-17 Added tool selection from config file. Added parametrized SpindelHolderAttach option for Z_Carriage
    [Cycl_Z_carriage.scad]
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2015-02-23 Fixed folder name and README
    [Cycl_Tapa_Electrónica.fcstd, Cycl_Tapa_Electrónica.stl, Cycl_acopleAspirador.stl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]
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2015-02-28 Fixed small render issue
    [Cycl_Z_carriage.scad]
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2015-09-25 Reverted L/R front rod idlers
    [Cycl_Y_frames.scad, Cycl_YfrontLeft_RodIdler.stl, Cycl_YfrontRight_RodIdler.stl]
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2015-09-26 Re-rendered gears (longer Z motor gear), Y linear bearing holders (zip-ties and nut support), Y rod idlers (corrected L/R), and Z carriage (additional screw holes)
    [Cycl_Electronic_case.stl, Cycl_Ycarriage_linearBearingHolder_x4.stl, Cycl_YfrontLeft_RodIdler.stl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]
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2015-09-26 Referenced the shorter version of the frames
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2015-12-16 Repair Rod Fixer
    [Cycl_rodFixer_x6.stl]
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2015-12-16 Repaired short frames
    [Cyclone_shortFrames.stl]
2016-02-17 Fixes tolerance for Z-axis gears.
    [Cycl_Z_carriage.scad]
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2017-08-27 Changed tolerance for rod- and motorgears to '0' to ensure a tight fit.
    [Cycl_X_frames.scad, Cycl_Y_frames.scad, Cycl_Z_carriage.scad]
2017-09-01 Generated new STLs for gears after tolerance fix
